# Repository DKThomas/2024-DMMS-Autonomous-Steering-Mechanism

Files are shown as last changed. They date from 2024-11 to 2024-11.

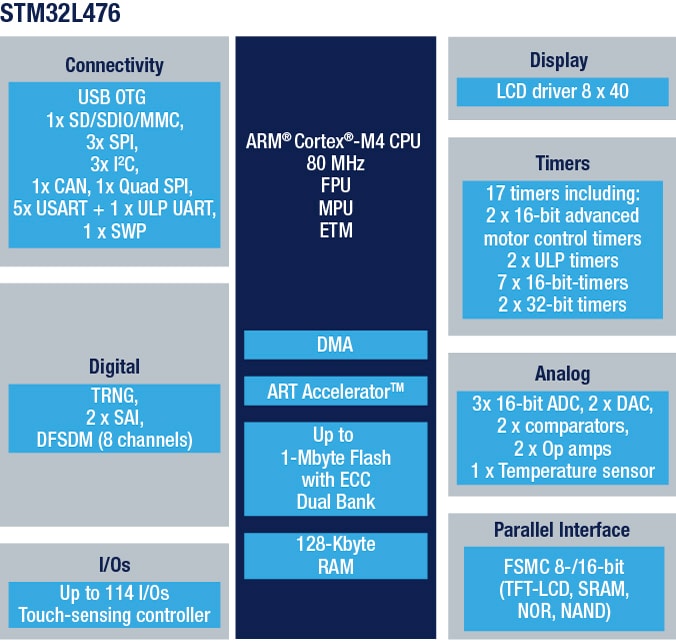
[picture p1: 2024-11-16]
Motor Control/NUCLEO-L476RG/STM32L476 Diagram.jpg

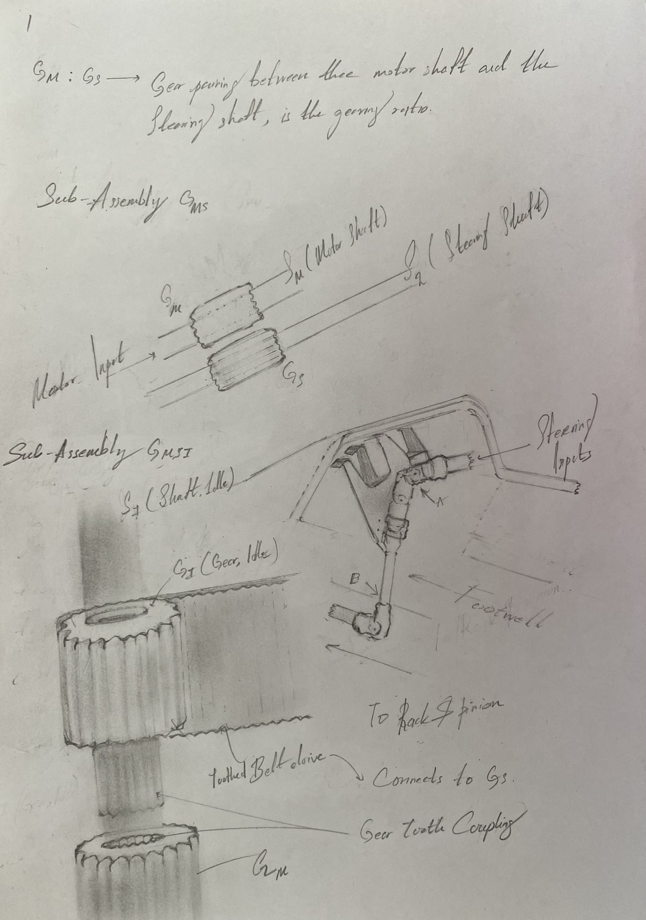
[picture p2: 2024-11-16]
Documentation/Ideation Sketches/Motor Mount/Sketch_v4.jpeg

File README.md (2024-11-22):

# **Project Overview**
Welcome to the repository for the project **Design of an autonomous steering mechanism for UTS Motorsports Autonomous** (**Project 29** by **Team 21** in **43019 Design in Mechanical and Mechatronic Systems** at **University of Technology Sydney** in **Spring 2024**). 

---

## **Folder Structure**

This repository is organized into three main folders:

### **`CAD/`**
This folder contains all CAD resources required for the project, including individual components, assembly files and installation guides.
- **`Enclosure/`**: CAD files for the protective housing of the system.
- **`FINAL design/`**: Finalized design files representing the complete system.
- **`Guide to Installation`**: Step-by-step guide for installing and assembling the mechanical system.
- **`Motor/`**: CAD models of the CubeMars AK80-9 motor.
- **`Motor Mount/`**: CAD models and technical drawings for mounting the motor.
- **`Template/`**: Driver template for compliance with FSAE rules.

### **`Documentation/`**
This folder provides insight to the development process of the project.
- **`Calculations/`**: Relevant calculations supporting the design.
- **`Competition Rules/`**: Official FSAE 2024 rules.
- **`Ideation Sketches/`**: Early conceptual sketches and ideas that led to the project’s development.
- **`Main Report`**: The primary report summarizing the project's goals, progress and results.
- **`Project Management/`**: Other project planning resources.
- **`Project Proposal`**: Initial proposal outlining the project's proposed objectives, scope, and deliverables.
- **`Reference Designs/`**: External design references used during the project’s development.

### **`Motor Control/`**
This folder focuses on the software and resources needed for motor control and implementation.
- **`AK Series Module Driver User Manual`**: User manual for the CubeMars AK series motors.
- **`Block Diagrams/`**: Visual representations of motor control architectures.
- **`Guide for CubeMars Motors`**: A practical guide for setting up and operating CubeMars motors.
- **`UTSMA_L476RG_STEERBYWIRE/`**: Source code for the motor control system for CAN communication using the STM32 NUCLEO-L476RG microcontroller.

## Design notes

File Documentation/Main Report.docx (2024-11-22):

# Autonomous Steering Mechanism

# Main Report

Client: UTS Motorsports

Detailed process documentation, including ideation, morphological table and scoring matrix to determine possible designs. This would be justified by calculations and drawings encapsulated in a report.

# Introduction

The project involves designing a mechatronic system which enables the steering mechanism on the 2022-2023 UTS Motorsports FSAE car to be controlled autonomously. The steering system consists of a steering wheel, universal joint linkages and a steering column into a worm drive steering rack.

The engineer must consider ergonomic constraints as the vehicle must be both manually and autonomously operated. Further, competition regulations must be kept in mind throughout the design process so the final solution can form part of a fully rules-compliant competition car.

Successful completion of this project allows this year’s team to migrate to the newer 2022/23 chassis and progress towards our goal of having a rules compliant autonomous Formula SAE car. The stakeholders involved include UTS Motorsports, UTS and team sponsors.

The proposed design composes of a BLDC mounted on a bracket onto the floor of the car, which is accompanied by a wedge which would help orient the motor to be parallel to the steering column. The motor is then connected via a series of gears and pulleys.

# Project Documentation

The project scope includes the following design documentation:

- Timeline
- Ideation
- Morphological Table
- Scoring Matrix

## Timeline

Below is a flow chart of the process we followed to achieve the final design.

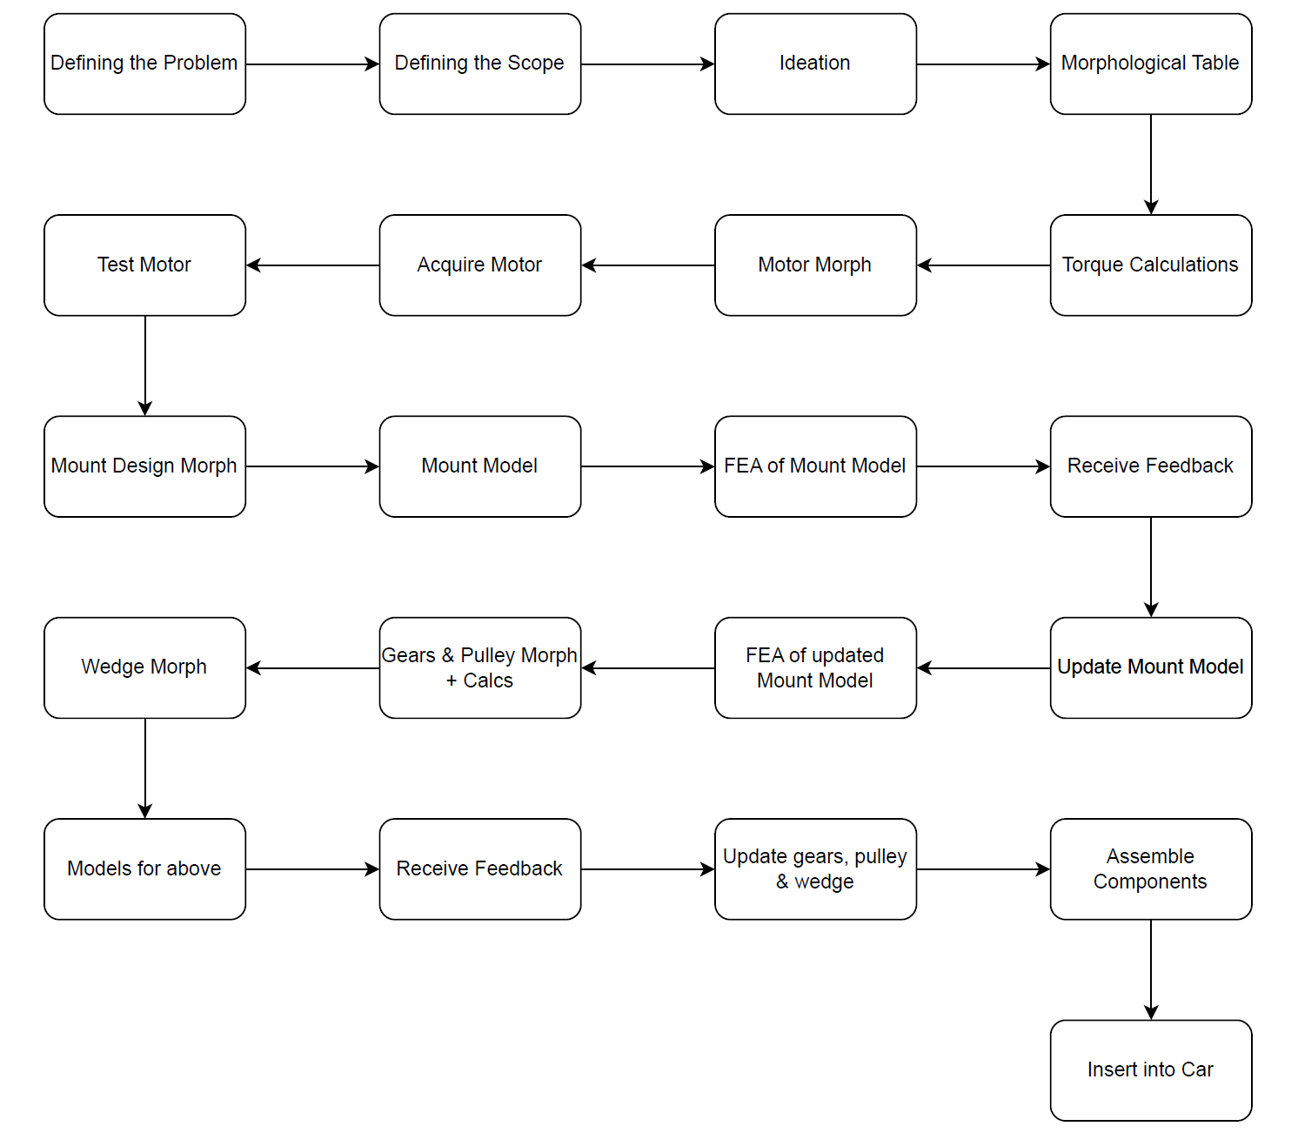
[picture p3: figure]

Figure 1: Timeline Flowchart

## Problem Statement

Design an electromechanical control system capable of rotating the steering column of the UTSMA autonomous car, ensuring it fits safely and ergonomically within the footwell while complying with the FSAE competition regulations.

## Ideation & Morphological Table

Ideating followed the basic principles of discussing how the product could be broken down into sub-assemblies which can be solved individually. These segments include:

### 1. Motor type

This was mainly condensed to two options: A BLDC or a Stepper. Finally, a BLDC Motor was selected: AK80-9.

### 2. Coupling Position

Positioned at the bottom of the steering column to make full use of space constraints with Cockpit Template (Refer to FSAE rules).

### 3. Motor to Steering Coupling

Belt and Pulley drive

### 4. Disengagement

Since the selected motor is backdrivable, the system can be electrically disengaged. Therefore, the considered idea of a mechanical disengage was discarded.

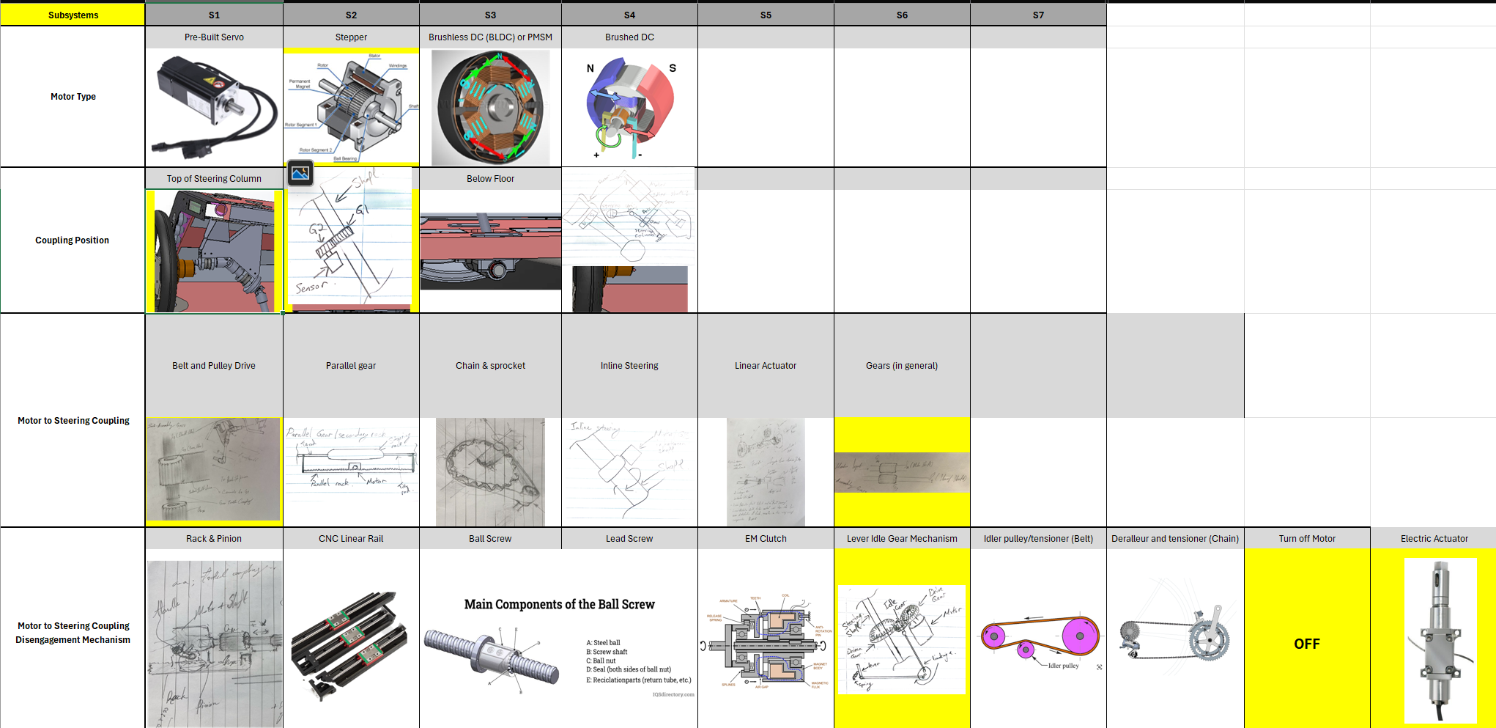
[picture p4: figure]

Figure 2: Morphological Table

## Scoring Matrix

Suitable and relevant components were selected from each of the morphological table categories and made into defined “designs”. This would be rated by the following criteria:

### 1. Performance

Delivering the calculated amount of torque without any compromise to the motor.

### 2. Precision & Accuracy

The ability of the steering system to precisely follow the desired path and make accurate adjustments.

### 3. Reliability & Durability

The system’s ability to consistently perform under various operating conditions and resist wear and tear.

### 4. Complexity & Integration

How easy the system is to design, implement, and integrate with the rest of the vehicle, including sensors, controllers, and other hardware.

### 5. Cost-Effectiveness

The overall cost of the steering system, including the cost of components, manufacturing, and maintenance.

### 6. Maintainability

The ease with which the system can be repaired, upgraded, or serviced.

### 7. Safety

Built-in safety features, fail-safes, and redundancy to prevent system failures from compromising the vehicle’s performance.

### 8. Modularity

Ease of create a modular variant, that is compliant with FSAE rules.

### 9. Scalability & Flexibility

Ease of using current design to be used in future iterations.

Using these criteria, the following design was proposed:

BLDC controlled using a magnetic rotary encoder (being positioned directly at the end of the motor shaft). It would be situated in the floor, driven by a set of gears and pulleys. The system can be disengaged by electrically disconnecting the motor, as it is backdrivable. This is shown in the figure below.

However, with a slight change in motors led to the sensor being discarded.

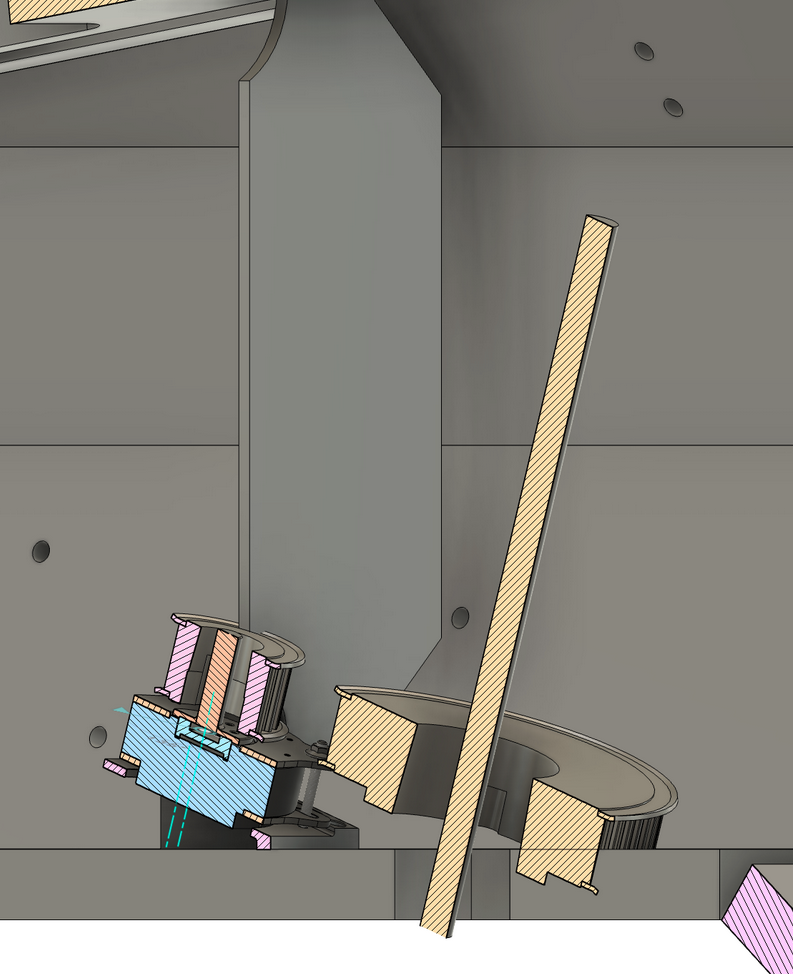
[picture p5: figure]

Figure 3: Mechanism fitted in Car Cockpit

# Issues & Feedback

- Motor torque calculations took a long time to confirm and validate, resulting in the team being able to purchase component (which has to be verified with tutor using calculations and confirmation from UTSMS) a couple of weeks in.
- Communications were not consistent in the first few weeks, which unfortunately was not completely resolved even by the end of the project.
- Issues with team members not showing up to meetings and not living up to agreements on time.
- Issues with final design not being in accordance with space constraints (refer to CAD and FSAE rules).
- Difficulty to come to decisions about final design.

# Design

## Pulley/Belt Design

This section covers the complete (for the most part) design for the belt and pulley system for the autonomous steering system.

### Determine Shaft diameters

From CAD model:

- Steering shaft column outer diameter: 15mm
- Steering shaft column inner diameter: 10mm

However, on the existing 2022 UTS Motorsports Electric car physical shaft, it is a solid 15mm steering column shaft.

Figure
CAD model close-up of shaft

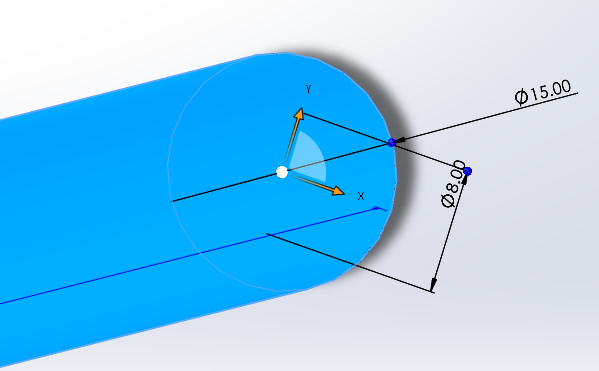
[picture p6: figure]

(Source: UTS Electric Motorsports, 2023)

Figure
Drawing of ’22 steering column

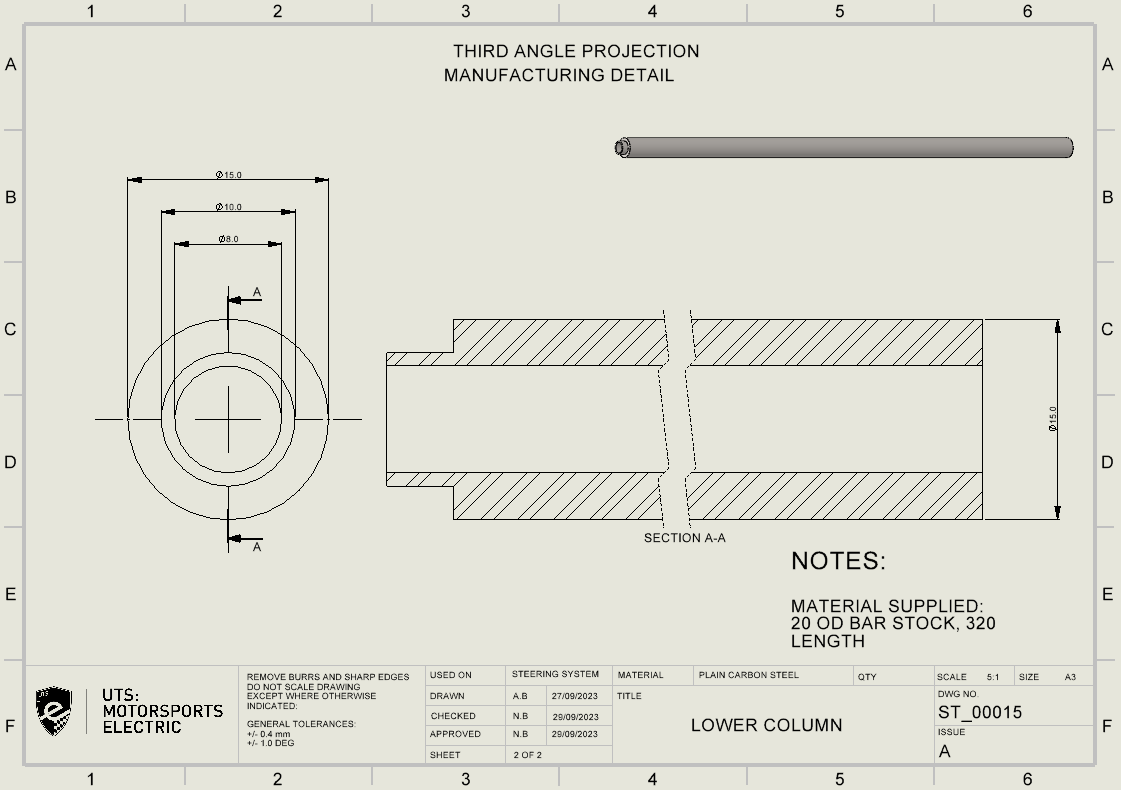
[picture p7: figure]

(Source: UTS Electric Motorsports, 2023)

From manual calculations and computer simulations:

Due to the lack of documentation, particularly with the design or the current steering system, step-by-step hand calculations were performed to analyse whether or not the current thickness of 15mm shaft diameter can support the motor’s torque. Please refer to “Analysis of Column Shaft” documentation.
Computer simulations in terms of finite element analysis (FEA) was performed to verify our hand calculations.

Motor shaft diameter:

The motor shaft of the AK1-9 motor will be customised to suit the mounting on the motor hub. The diameter of the shaft will be determined by both torsion, radial forces, along with axial forces.

Figure
Picture of AK10-9 V2.0

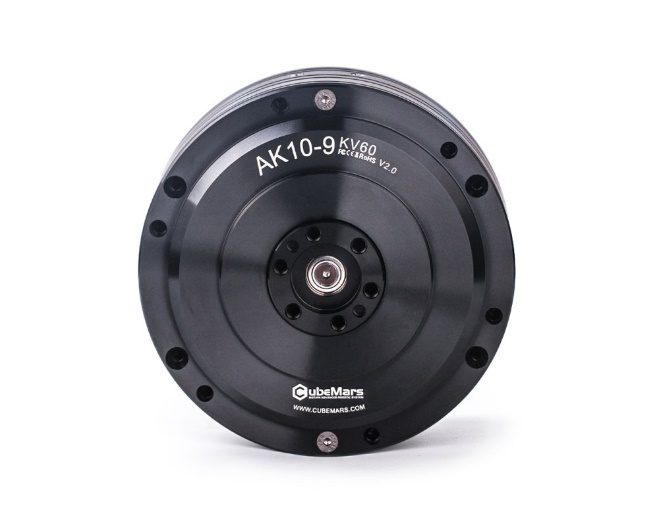
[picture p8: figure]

(Source: Tmotor, n.d)

Manual calculations and computer simulations:

Both hand calculations and FEA were performed on the design of the motor shaft. Please refer to “Analysis of Column Shaft” documentation.

### Belt Selection

There are several types of pulley belts available such as flat, V, Wedge, Synchronous belts along with other types.

Table
Comparison of Belt performance

(Source: Childs, Peter R.N.. (2014). Mechanical Design Engineering Handbook. Elsevier)

Figure
Various Belt Cross Sections

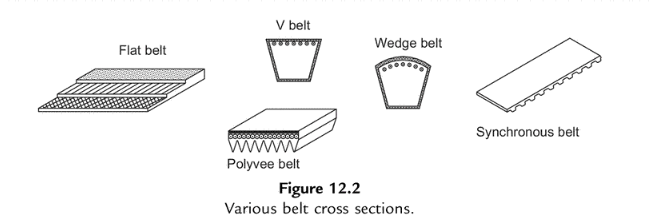
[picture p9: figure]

(Various Belts - Source: Childs, Peter R.N.. (2014). Mechanical Design Engineering Handbook. Elsevier)

Referring to the Table 12.1, synchronous belts can output an optimum efficiency of up to 98%, due to their teeth engagement between the belt teeth and the grooves of the pulley. Due to the required precise motion control of an autonomous steering system, a slippage between the belt and the pulley is highly not preferred, which the synchronous belt as the name suggests provides exact shaft synchronization (with the exception of belt creep).
Synchronous belts need significantly lower installation tension compared to V-belts, which results in reduced stress on drive components like shafts and bearings. Hence, along with the Figure 12.4, synchronous belt has been selected.

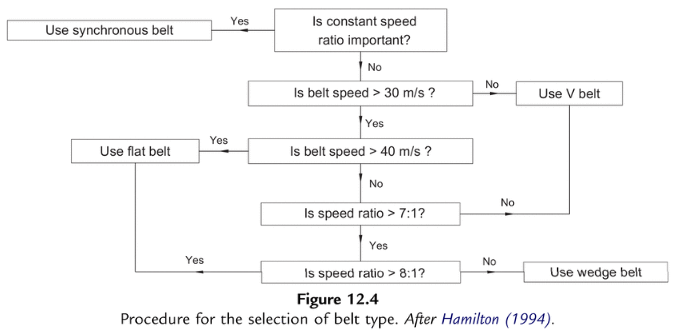
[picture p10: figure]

### General Selection Procedure – Synchronous belt pulley system

#### Define the rotational speeds of the motor shafts.

Rated motor (AK10-9 V2) speed:

- 228 rpm at 18nm (rated torque)

24.9N Steering force (With Factor of Safety of 1.5 from 16.6N steering force):
- ~200 rpm at 25nm

Motor Analysis Chart:

### 1) Pulley selection

Table
Motor Analysis Chart

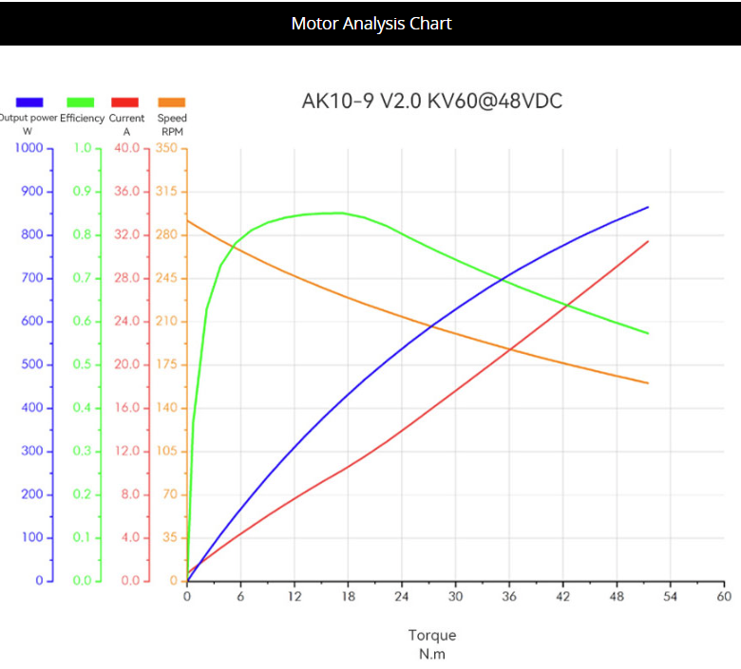
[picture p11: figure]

(Source: Tmotor, n.d)

N.m to hp:

P(HP)=(T(Nm)×N(RPM))/7127

For 18nm:

P(HP)=(18(Nm)×228(RPM))/7127 = 0.576HP

For 25nm:

P(HP)=(25(Nm)×200(RPM))/7127 = 0.702 HP

### 2) Determine the service factor.

Using Table 7-8 below, using good engineering judgement, a service factor of 1.2 has been selected.

Table
Synchronous Belt Service Factor Table

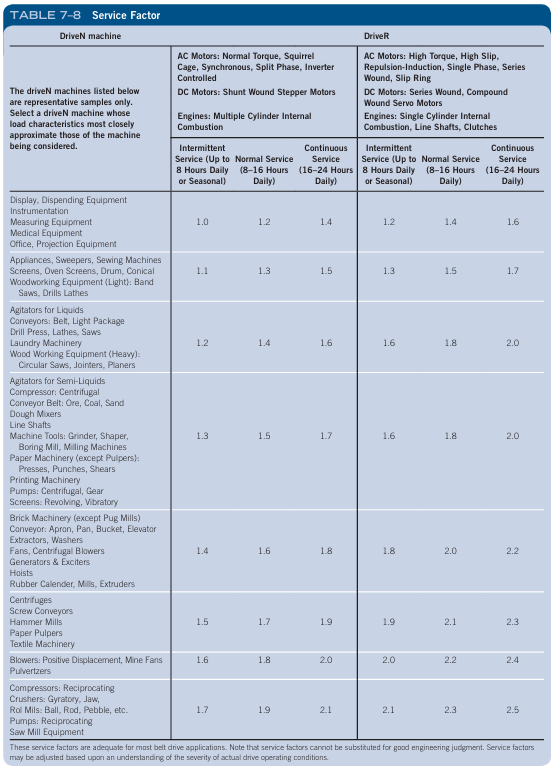
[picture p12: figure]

(Source: Mott, Robert L, 2018)

### 3) Calculate the design power.

Using the formula above;

- the design rated power is = 0.576HP x 1.2 = 0.691 HP (0.691 x 0.7457 = 0.52 kW)
- the design peak power is = 0.702 HP x 1.2 = 0.8424 HP (0.8424 x 0.7457 = 0.63kW)

1. Determine required pitch of the belt.

Graph
GT Belt Selection Guide

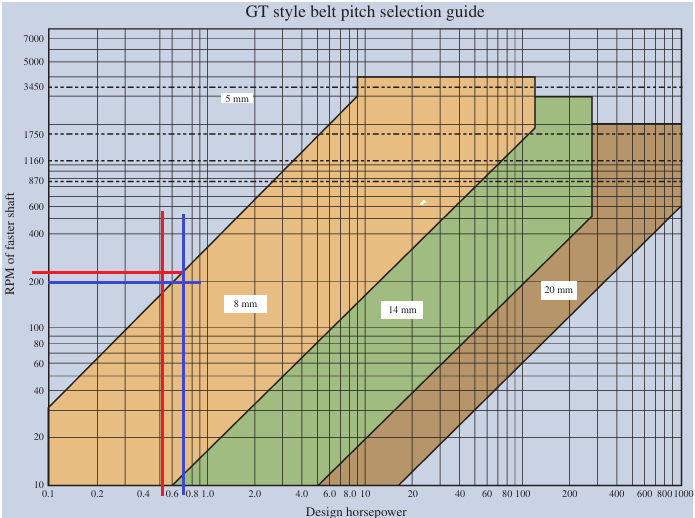
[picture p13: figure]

(Source: Mott, Robert L, 2018)

Using the table above, the red lines depict the selection for the rated torque, whilst the blue lines indicate the use of peak torque. Since the majority of the imaginary curve from the red line intersection to the blue line intersection, a 5mm belt pitch would be considered a reasonable design choice. However, 8mm had to be chosen due to belt selection requirements.

2. Determine the velocity ratio VR belt between the driver and driven sprockets.

To determine the sizes/ratio of the driven and driver pulleys, giving the following:

Motor operational torque: 18nm
Required torque: 24.9nm

An adequate pulley size ratio is needed to meet the steering force requirement of 24.9nm.

As the torque ratio is directly related to the velocity ratio:

Torque ratio = (Torque Required (Driven))/(Motor Torque (Driver))

Using the values of 24.9nm of steering torque (with FOS 1.5), with 24.9nm of required torque,

Torque ratio = (24.9 nm)/(24.9nm) ≈ 1

Therefore the driven pulley (on steering column shaft) must be 1 or more greater than the driver pulley (on the motor).

When the car is in motion, using a dynamic torque of 27nm (from 13.5N x FOS 2), At moderate dynamic or during sudden spikes:

Motor rated torque: 18nm
Required torque: 27nm

Torque ratio = (27 nm)/(18nm) ≈ 1.5

Thus, the driven pulley (attached to the steering column shaft) needs to be at least 1.38 times larger than the driver pulley (connected to the motor).

8mm Pitch Belt:

Table
Screenshot of 8mm Synchronous Belt Drive Table Part 1

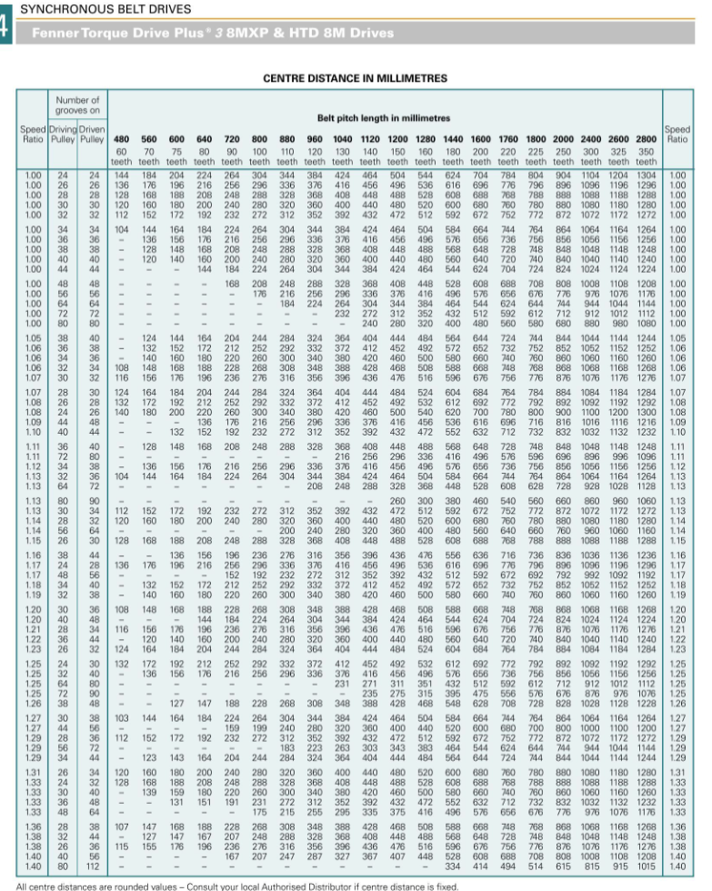
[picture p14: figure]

(Source: Fenner, 2006)

Table
Screenshot of 8mm Synchronous Belt Drive Table Part 2

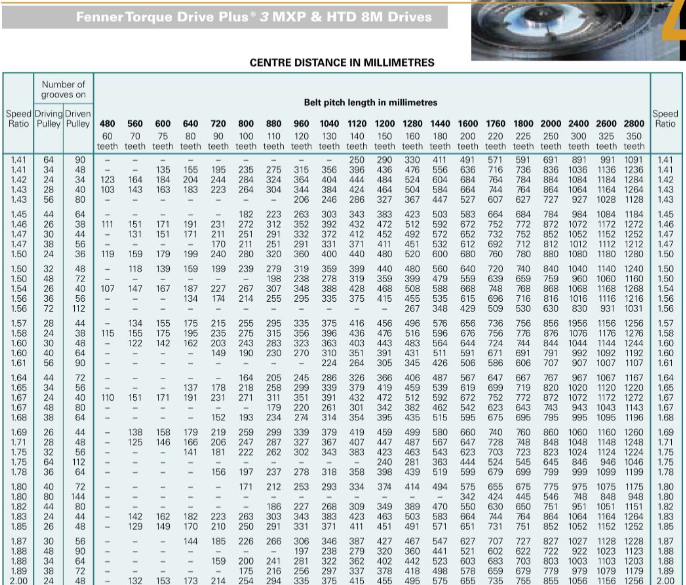
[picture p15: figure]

(Source: Fenner. 2006)

43019 DMMS T21 - P29 - Autonomous Steering Mechanism 15 Nov 2024

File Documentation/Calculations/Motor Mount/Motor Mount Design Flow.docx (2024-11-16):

Whitney, C. (2005, October 25). Sliding Motor Mount. FineWoodworking; Fine Woodworking. https://www.finewoodworking.com/2005/10/25/sliding-motor-mount

Supporting documentation for developing a Sliding Motor Mount.

Conceptual design of automobile engine rubber mounting composite using TRIZ-Morphological chart-analytic network process technique. (2018). Defence Technology, 14(4), 268–277. https://doi.org/10.1016/j.dt.2018.05.009

Information extracted (referred pages; pg. 266-270, pg. 273-275):

(1) Need for the usage (purpose) of rubber mounting – vibration dampening.

(2) Considerations when selecting material.

(3) Considerations when selecting mounting; This includes whether: (a) if a mounting is necessary,

(b) if YES, what are the relevant design/selection criteria (i.e., performance, weight, cost & etc)

(4) Criteria for weighing conceptual design (opt.)

Khan, A., Razlee, A., Zainal Nazri, Razak, A., & Ahmad, M. N. (2022). Topology Optimization of an Engine Mounting Bracket Using Finite Elements. Advanced Structured Materials, 243–254. https://doi.org/10.1007/978-3-030-93250-3_21

Information extracted (referred “Introduction”; pg. 1)

(1) FEA vs EMA
(2) Topology Optimization

(3) “x” Mount to be able to withstand, “x” load, “x” vibration/frequency.

Design and Construction of Motor Mounts. (2008). https://roblab.org/theses/2008-REV-Motor-Tan.pdf

Information extracted (referred pages; pg. 5-7, pg. 17-20. pg. 21-36):

(1) Further discussion on rubber mounting. This report discusses the general integration of rubber mounts for an engines & motors – To Dampen any resultant (BLDC) motor vibration and isolate these vibrations from the chassis.

(2) Assembly of rear support mounts, front support mounts & coupling.

(2.1) Depending on the motor, select a suitable mount design (i.e., middle-style, plate mounts)

(2.2) Motor front mounting plate/adapter design process + CNC machined, for precision using Al13.

(2.3) Coupling – TAPER LOCK HUBS (favoured) due to coupling security + ease of maintenance.

Look here for in-market options: https://www.ptparts.com.au/products/category/JADNKLMX-special-hubs/N100-TL-J-HUB--taper-lock-hubs

(3) Design options + ideation + finalisation of design (pg.)

Galloway, K. C., G. Clark Haynes, Deniz Ilhan, & Koditschek, D. (2010, November 4). X-RHex: A Highly Mobile Hexapedal Robot for Sensorimotor Tasks. ResearchGate; unknown. https://www.researchgate.net/publication/49128188_X-RHex_A_Highly_Mobile_Hexapedal_Robot_for_Sensorimotor_Tasks/figures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

Information extracted (referred pages; pg. 7-10):

(1) Spring loaded quick-release latches.
(2) Gearing offsets (opt.).

(3) Motor shaft extension.
(4) Overall motor mount design that consists of the assembly of a back plate & front plate.

Motor Mount Design Examples

1. Ideation of mounting system
2. Ideation of subsystem(s) + subsystem breakdown
2.1 Force distribution considerations (system suited to handle lateral and vertical loads)
2.1.1 Calculations/justifications for 2.1 – TBD
2.2 Decision to use tilted + angled Mount_Legs to distribute load(s) over a wider area.
2.2.1 Angle of 70 degrees, between Motor_Base_Plate & Mount_Legs (for optimal load distribution)
2.2.2 Calculations/justifications for 2.2.1 – TBD
2.2.3 FIND; Angle of ‘x’ for tilt – TBD
2.3 ALL req. dimensions for Motor_Base_Plate & Mount_Legs – TBD
2.3.1 Motor_Base_Plate “material selection” (6061, Al) – TDB; shy 2
2.3.1.1 Motor_Base_Plate spec. re-evaluation
2.3.2 Mount_Legs “material selection”
2.3.2.1 Mount_Legs spec. re-evaluation
2.4 Decision to design the Motor_Base_Plate separately + mount to Mount _Legs (for ease of handling)
2.4.1 Mounting Motor_Base_Plate to Mount _Legs
Using: External_Slotted_Flange + *Bolts + *Lock nuts + *Washers (Nord-Lock)
2.4.2 External_Slotted_Flange to be supported with Gusset_Plate(s)
2.4.3 External_Slotted_Flange with “vertical/horizontal slot” + “slot dimensions” – TBD
2.4.5 External_Slotted_Flange dimensions – TDB
2.4.4 External_Slotted_Flange “material selection” (100% infill, PLA) – TDB; shy 2
2.4.4.1 External_Slotted_Flange spec. re-evaluation
2.4.5 Gusset_Plate(s) dimensions – TDB
2.4.6 Gusset_Plate(s) “material selection” (100% infill, PLA) – TDB; shy 2
2.4.6.1 Gusset_Plate(s) spec. re-evaluation
2.4.7 *Bolts selection (for fastening Motor_Base_Plate to External_Slotted_Flange) – TBD
2.4.8 *Bolts; quantity + dimensions – TBD
2.4.9 *Lock nuts; quantity + dimensions – TBD
2.4.10 *Washers; quantity + dimensions – TBD
2.4.11 Calculations/justifications for 2.4.7 + 2.4.8 + 2.4.9 + 2.4.10 – TBD
Component List (Not complete):
Motor_Base_Plate, Mount_Legs, Motor_Base_Plate, External_Slotted_Flange, Gusset_Plate(s), *Bolts; MotorToBase_Plate_Bolt, Base_PlateToMount_Leg_Bolt, Mount_LegToFloor_Bolt *Lock nuts, *Washers

Stamp 1: Steps 1. – 5. Finding Belt Length (Distance between Motor_Shaft & Steering_Shaft)
1. Find Rated Motor torque
2. Find Req. Steering (Rack & Pinion) torque
3. Calculate “optimum pulley ratio”
4. Find Req. “Motor_Shaft_Pulley pitch + diameter” using 3.
4.1 Find Req. “Steering_Shaft_Pulley pitch + diameter” Using 3.
4.1.2 Hence; Req. “Motor_Shaft_Pulley teeth quantity”. Using 3.
4.1.3 Hence; Req. “Steering_Shaft_Pulley teeth quanitity”. Using 3.
5. Find the belt length. Therefore; “viable Motor – Steering_Shaft distance” using belt length formula (https://sudenga.com/resources/figuring-belt-lengths-and-distance-between-pulleys/)
Stamp 2: Finding Optimum Belt Parameters & Dimensions
6. Find suitable belt specifications using information in 5.
6.1 Find “belt width” – TBD
6.2 Find quanitity of “belt teeth” – TBD
6.3 Finalise belt selection – TBD

(Custom) Motor Mount Design Flow

Motor_Shaft & Steering_Shaft – Assembly

Stamp 3: Confirming Motor_Base_Plate + Mount_Legs Assembly & Positioning

7. Decide Mount_Legs “mounting position” on vehicle floor. Using 5. – TBD
8. Find Req. “motor mounting position” on Motor_Base_Plate – TBD
9. Find Req. Motor_Base_Plate “mounting position”between the Mount_Legs
10. Model motor mount + Perform FEA + CAD for Motor mount.
11. Confirm ALL “motor mounting positions”
Stamp 1: Finding Tensioner Specifications, Design & Requirements
1. Find Req. “tensioning position” (position along the belt that needs tensioning) along pulley belt
2. Tensioner specifications (temporary, Req. Tensioner_Pulley parameters). Consider info from 7.
2.1 (Justify) IS Tensioner mounted on “car_floor/motor_mount” – TBD
2.1.1 Confirms Req. Tensioner_Pulley placement along belt – TBD
2.2 Confirms Req.Tensioner_Pulley parameters – TBD
2.2.1 Tensioner_Pulley dimensions + “material selection” – TBD
2.3 Tensioner “adjustable/spring-loaded” – TBD
Stamp 2: Tensioner_Mount Design – Brief overview
2.4 Tensioner_Pulley to Tensioner_ Mount force distribution – TBD
2.5 Tensioner_ Mount “mounting position” on (+ using) outcome of 2.1 & 2.1.1

Tensioner Specifications – Brief

Pulley Design

Distance between Motor_Shaft & Steering_Shaft: https://sudenga.com/resources/figuring-belt-lengths-and-distance-between-pulleys/

Pulley & Belt calculator https://www.blocklayer.com/pulley-belt

Pulley ratio & RPM calculator: https://calculator.academy/pulley-size-calculator/

Pulley Design: https://assets-global.website-files.com/6321faa31729834cada9ee26/6321faa317298319abaa1420_B107%20Pulley%20Design%20Guidelines%2C%20Material%20and%20Finishes.pdf

Next stages – Brief overview:
Motor_Shaft req. dimensions.
Motor to Motor_Shaft *coupling
Calculations for forces acting on Motor_Shaft
(opt.) Motor_Shaft dimension + spec. re-evaluation
Motor_Shaft_InFloor_Bearing spec

Ideation Process for Motor Mounting Mechanisms (Most preferred iteration – See below; circled in RED)

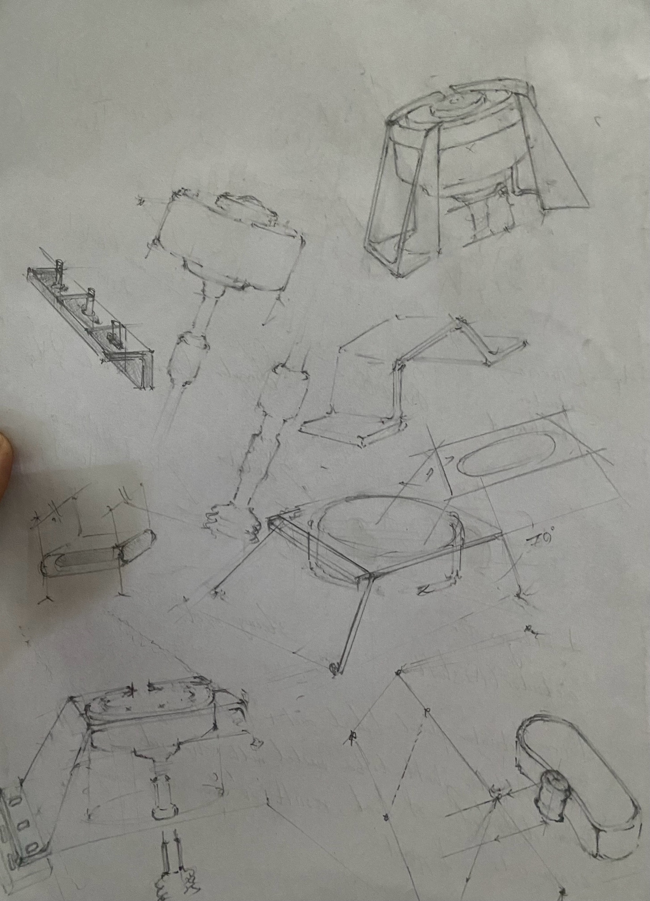
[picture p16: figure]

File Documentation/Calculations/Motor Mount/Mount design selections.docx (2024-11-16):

## Motor Mounting:

Option 1 – Angled mount (adjustable) with motor facing downwards, hole in the floor with a bearing:

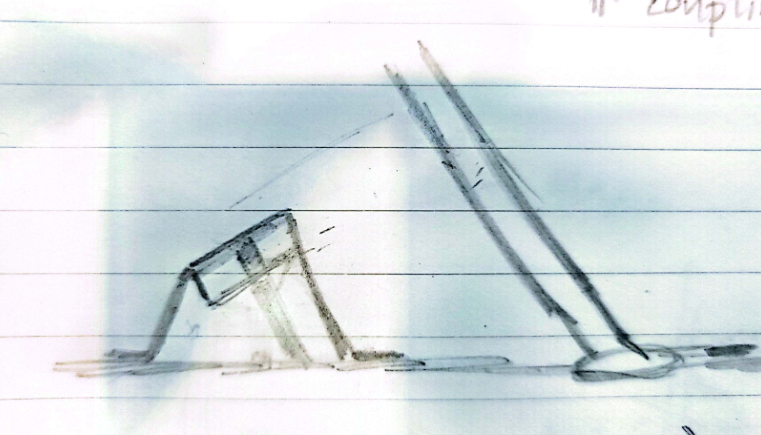
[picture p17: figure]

Option 2: Parallel mount (adjustable), motor facing downwards, U-joint with bearing (Information, despite the detail presented on the sketch below, it is important to note that the motor will be mounted atop the base mount)

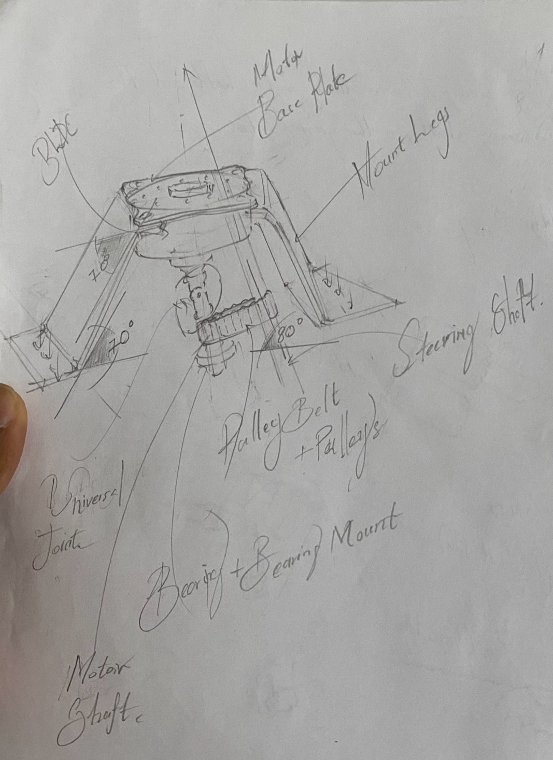
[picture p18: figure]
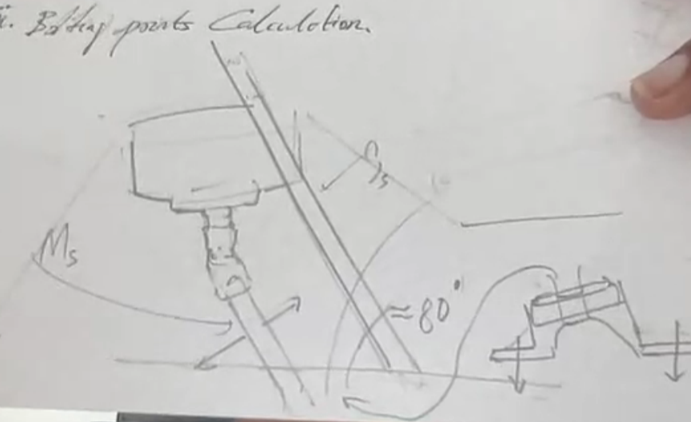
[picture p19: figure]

Option 3: Angled mount (adjustable) motor facing upwards.

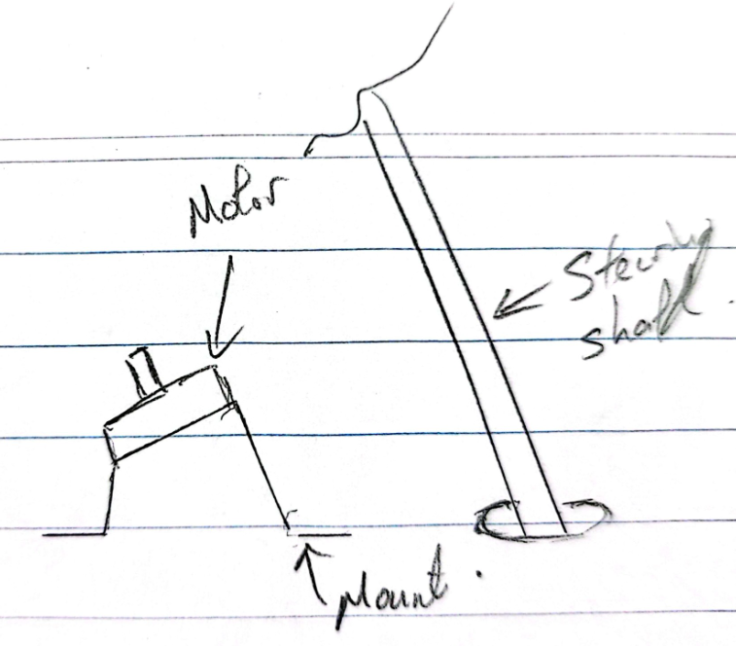
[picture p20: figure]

## Adjustable Mechanism:

Option 1:

Option 2:

Option 3:

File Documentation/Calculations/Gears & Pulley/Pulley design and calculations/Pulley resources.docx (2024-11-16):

Solidworks Belt tutorial:

https://www.youtube.com/watch?v=J5c3EpZYS3Y

https://www.youtube.com/watch?v=hBewTs1fLto

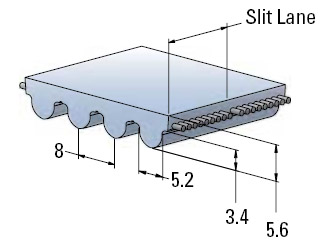
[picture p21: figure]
Dimensional drawing

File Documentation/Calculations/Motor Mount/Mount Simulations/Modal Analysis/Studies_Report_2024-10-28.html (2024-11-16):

Image Width (pixels):

# Study Report

Analyzed File | Mount_Legs v3_Mod v2 v90
Version | Autodesk Fusion (2.0.20494)
Creation Date | 2024-10-28, 17:47:54
Author | dulnethweerasinghe

#### Report Properties

Title | Studies
Author | dulnethweerasinghe

## Simulation Model 1

### Study 10 - Modal Frequencies

##### Study Properties

Study Type | Modal Frequencies
Last Modification Date | 2024-10-28, 15:54:26

#### Settings

##### General

Contact Tolerance | 0.05 mm
Number of Modes | 12
Frequency Range [Hz] | 5-50
Compute Preloaded Modes | Yes

##### Mesh

Average Element Size (% of model size)
Solids | 4
Scale Mesh Size Per Part | Yes
Average Element Size (absolute value) | -
Element Order | Parabolic
Create Curved Mesh Elements | Yes
Max. Turn Angle on Curves (Deg.) | 25
Max. Adjacent Mesh Size Ratio | 1.5
Max. Aspect Ratio | 10
Minimum Element Size (% of average size) | 10

##### Adaptive Mesh Refinement

Number of Refinement Steps | 2
Results Convergence Tolerance (%) | 20
Frequency Mode | 12

#### Materials

Component | Material | Safety Factor
Body2 | Steel, Mild | Yield Strength
Indented Hex Flange Head Machine Screw ANSI B18.6.7M - M5x0.8 x 40 Steel Grade 2 Plain v1:1 | Steel Grade 2, Plain | Yield Strength
Indented Hex Flange Head Machine Screw ANSI B18.6.7M - M5x0.8 x 40 Steel Grade 2 Plain v1:2 | Steel Grade 2, Plain | Yield Strength
Indented Hex Flange Head Machine Screw ANSI B18.6.7M - M5x0.8 x 40 Steel Grade 2 Plain v1:3 | Steel Grade 2, Plain | Yield Strength
Indented Hex Flange Head Machine Screw ANSI B18.6.7M - M5x0.8 x 40 Steel Grade 2 Plain v1:4 | Steel Grade 2, Plain | Yield Strength
Hex Flange Nut ANSI B18.2.4.4M - M5 x 0.8 Steel Grade 2H Plain v1:1 | Steel Grade 2H, Plain | Yield Strength
Hex Flange Nut ANSI B18.2.4.4M - M5 x 0.8 Steel Grade 2H Plain v1:2 | Steel Grade 2H, Plain | Yield Strength
Hex Flange Nut ANSI B18.2.4.4M - M5 x 0.8 Steel Grade 2H Plain v1:3 | Steel Grade 2H, Plain | Yield Strength
Hex Flange Nut ANSI B18.2.4.4M - M5 x 0.8 Steel Grade 2H Plain v1:4 | Steel Grade 2H, Plain | Yield Strength

##### Steel Grade 2, Plain

Density | 7.750E-06 kg / mm^3
Young's Modulus | 210000.00 MPa
Poisson's Ratio | 0.30
Yield Strength | 393.00 MPa
Ultimate Tensile Strength | 510.00 MPa
Thermal Conductivity | 0.056 W / (mm C)
Thermal Expansion Coefficient | 1.200E-05 / C
Specific Heat | 480.00 J / (kg C)

##### Steel Grade 2H, Plain

Density | 7.750E-06 kg / mm^3
Young's Modulus | 210000.00 MPa
Poisson's Ratio | 0.30
Yield Strength | 393.00 MPa
Ultimate Tensile Strength | 510.00 MPa
Thermal Conductivity | 0.056 W / (mm C)
Thermal Expansion Coefficient | 1.200E-05 / C
Specific Heat | 480.00 J / (kg C)

##### Steel, Mild

Density | 7.850E-06 kg / mm^3
Young's Modulus | 220000.00 MPa
Poisson's Ratio | 0.275
Yield Strength | 207.00 MPa
Ultimate Tensile Strength | 345.00 MPa
Thermal Conductivity | 0.045 W / (mm C)
Thermal Expansion Coefficient | 1.200E-05 / C
Specific Heat | 480.00 J / (kg C)

#### Contacts

#### Mesh

Type | Nodes | Elements
Solids | 284087 | 159634

#### Load Case1

 Solve result of this load case is out of date.

#### Constraints

##### Fixed1

Type | Fixed
Ux | Fixed
Uy | Fixed
Uz | Fixed

###### Selected Entities

For correct interpretation of this image use e.g. IE9, Chrome, Safari, Firefox

#### Loads

##### Gravity

Type | Gravity
Magnitude | 9.807 m / s^2
X Value | 0.00 m / s^2
Y Value | 0.00 m / s^2
Z Value | -9.807 m / s^2

###### Selected Entities

For correct interpretation of this image use e.g. IE9, Chrome, Safari, Firefox

#### Results

##### Result Summary

Frequency | Participation X | Participation Y | Participation Z
Mode 1: 352.514 Hz | 53.7701011 | 0 | 0.0032

##### Total Modal Displacement

###### Mode 1: 352.514 Hz Total Modal Displacement

0.00 1.00

For correct interpretation of this image use e.g. IE9, Chrome, Safari, Firefox

Image Width (pixels):

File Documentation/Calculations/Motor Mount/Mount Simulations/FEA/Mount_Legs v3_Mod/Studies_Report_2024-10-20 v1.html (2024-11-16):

Image Width (pixels):

# Study Report

Analyzed File | Mount_Legs v3_Mod v4
Version | Autodesk Fusion (2.0.20476)
Creation Date | 2024-10-20, 01:47:26
Author | dulnethweerasinghe

#### Report Properties

Title | Studies
Author | dulnethweerasinghe

## Simulation Model 1

### Study 6 - Static Stress

##### Study Properties

Study Type | Static Stress
Last Modification Date | 2024-10-20, 01:38:45

#### Settings

##### General

Contact Tolerance | 0.05 mm
Remove Rigid Body Modes | No

##### Mesh

Average Element Size (% of model size)
Solids | 3
Scale Mesh Size Per Part | No
Average Element Size (absolute value) | -
Element Order | Parabolic
Create Curved Mesh Elements | No
Max. Turn Angle on Curves (Deg.) | 60
Max. Adjacent Mesh Size Ratio | 1.5
Max. Aspect Ratio | 10
Minimum Element Size (% of average size) | 20

##### Adaptive Mesh Refinement

Number of Refinement Steps | 0
Results Convergence Tolerance (%) | 20
Portion of Elements to Refine (%) | 10
Results for Baseline Accuracy | von Mises Stress

#### Materials

Component | Material | Safety Factor
Body2 | Aluminum 6061 | Yield Strength
Indented Hex Flange Head Machine Screw ANSI B18.6.7M - M6x1 x 20 Steel Grade 2 Plain v1:2 | Steel Grade 2, Plain | Yield Strength
Indented Hex Flange Head Machine Screw ANSI B18.6.7M - M6x1 x 20 Steel Grade 2 Plain v1:3 | Steel Grade 2, Plain | Yield Strength
Indented Hex Flange Head Machine Screw ANSI B18.6.7M - M6x1 x 20 Steel Grade 2 Plain v1:4 | Steel Grade 2, Plain | Yield Strength
Indented Hex Flange Head Machine Screw ANSI B18.6.7M - M6x1 x 20 Steel Grade 2 Plain v1:1 | Steel Grade 2, Plain | Yield Strength

##### Steel Grade 2, Plain

Density | 7.750E-06 kg / mm^3
Young's Modulus | 210000.00 MPa
Poisson's Ratio | 0.30
Yield Strength | 393.00 MPa
Ultimate Tensile Strength | 510.00 MPa
Thermal Conductivity | 0.056 W / (mm C)
Thermal Expansion Coefficient | 1.200E-05 / C
Specific Heat | 480.00 J / (kg C)

##### Aluminum 6061

Density | 2.700E-06 kg / mm^3
Young's Modulus | 68900.00 MPa
Poisson's Ratio | 0.33
Yield Strength | 275.00 MPa
Ultimate Tensile Strength | 310.00 MPa
Thermal Conductivity | 0.167 W / (mm C)
Thermal Expansion Coefficient | 2.360E-05 / C
Specific Heat | 897.00 J / (kg C)

#### Contacts

##### Bonded

Name

[S] Bonded5 [Simulation Model 1:1||Indented Hex Flange Head Machine Screw ANSI B18.6.7M - M6x1 x 20 Steel Grade 2 Plain v1:4]

[S] Bonded6 [Simulation Model 1:1||Indented Hex Flange Head Machine Screw ANSI B18.6.7M - M6x1 x 20 Steel Grade 2 Plain v1:3]

[S] Bonded7 [Simulation Model 1:1||Indented Hex Flange Head Machine Screw ANSI B18.6.7M - M6x1 x 20 Steel Grade 2 Plain v1:2]

[S] Bonded8 [Simulation Model 1:1||Indented Hex Flange Head Machine Screw ANSI B18.6.7M - M6x1 x 20 Steel Grade 2 Plain v1:1]

[S] Bonded10 [Simulation Model 1:1||Indented Hex Flange Head Machine Screw ANSI B18.6.7M - M6x1 x 20 Steel Grade 2 Plain v1:4]

[S] Bonded11 [Simulation Model 1:1||Indented Hex Flange Head Machine Screw ANSI B18.6.7M - M6x1 x 20 Steel Grade 2 Plain v1:1]

#### Mesh

Type | Nodes | Elements
Solids | 108271 | 63075

#### Load Case1

#### Constraints

##### Fixed1

Type | Fixed
Ux | Fixed
Uy | Fixed
Uz | Fixed

###### Selected Entities

For correct interpretation of this image use e.g. IE9, Chrome, Safari, Firefox

#### Loads

##### Gravity

Type | Gravity
Magnitude | 9.807 m / s^2
X Value | 0.00 m / s^2
Y Value | 0.00 m / s^2
Z Value | -9.807 m / s^2

###### Selected Entities

For correct interpretation of this image use e.g. IE9, Chrome, Safari, Firefox

##### Force1

Type | Force
Magnitude | 8.00 N
X Value | 0.00 N
Y Value | 0.00 N
Z Value | -8.00 N
Force Per Entity | No

###### Selected Entities

For correct interpretation of this image use e.g. IE9, Chrome, Safari, Firefox

##### Moment1

Type | Moment
Magnitude | 20000.00 N mm
X Value | 0.00 N mm
Y Value | 0.00 N mm
Z Value | -20000.00 N mm
X Angle | 0.0 deg
Y Angle | 90.0 deg
Z Angle | 0.0 deg

###### Selected Entities

For correct interpretation of this image use e.g. IE9, Chrome, Safari, Firefox

##### Moment2

Type | Moment
Magnitude | 20000.00 N mm
X Value | 0.00 N mm
Y Value | 0.00 N mm
Z Value | -20000.00 N mm
X Angle | 0.0 deg
Y Angle | 90.0 deg
Z Angle | 0.0 deg

###### Selected Entities

For correct interpretation of this image use e.g. IE9, Chrome, Safari, Firefox

#### Results

##### Result Summary

Name | Minimum | Maximum
Safety Factor
Safety Factor (Per Body) | 4.819 | 15.00
Stress
von Mises | 0.01 MPa | 57.07 MPa
1st Principal | -34.019 MPa | 92.325 MPa
3rd Principal | -86.913 MPa | 35.275 MPa
Normal XX | -75.346 MPa | 81.357 MPa
Normal YY | -46.568 MPa | 48.774 MPa
Normal ZZ | -43.483 MPa | 44.66 MPa
Shear XY | -19.922 MPa | 19.801 MPa
Shear YZ | -12.539 MPa | 19.236 MPa
Shear ZX | -25.756 MPa | 20.067 MPa
Displacement
Total | 0.00 mm | 0.051 mm
X | -0.03 mm | 0.025 mm
Y | -0.024 mm | 0.032 mm
Z | -0.031 mm | 0.033 mm
Reaction Force
Total | 0.00 N | 89.701 N
X | -80.565 N | 69.68 N
Y | -34.406 N | 29.424 N
Z | -36.039 N | 41.484 N
Strain
Equivalent | 0.00 | 0.001
1st Principal | -2.131E-07 | 0.001
3rd Principal | -0.001 | 0.00
Normal XX | -7.805E-04 | 8.154E-04
Normal YY | -2.110E-04 | 2.472E-04
Normal ZZ | -2.122E-04 | 2.136E-04
Shear XY | -7.691E-04 | 7.644E-04
Shear YZ | -4.841E-04 | 3.686E-04
Shear ZX | -7.641E-04 | 7.495E-04
Contact Pressure
Total | 0.00 MPa | 21.643 MPa
X | -13.313 MPa | 18.089 MPa
Y | -20.048 MPa | 9.159 MPa
Z | -8.654 MPa | 17.217 MPa
Contact Force
Total | 0.00 N | 9.094 N
X | -5.931 N | 5.789 N
Y | -3.795 N | 2.059 N
Z | -8.942 N | 7.76 N

##### Safety Factor

###### Safety Factor (Per Body)

0.00 8.00

For correct interpretation of this image use e.g. IE9, Chrome, Safari, Firefox

##### Stress

###### von Mises

[MPa] 0.01 57.07

For correct interpretation of this image use e.g. IE9, Chrome, Safari, Firefox

###### 1st Principal

[MPa] -34.019 92.325

For correct interpretation of this image use e.g. IE9, Chrome, Safari, Firefox

###### 3rd Principal

[MPa] -86.913 35.275

For correct interpretation of this image use e.g. IE9, Chrome, Safari, Firefox

##### Displacement

###### Total

[mm] 0.00 0.051

For correct interpretation of this image use e.g. IE9, Chrome, Safari, Firefox

#### Load Case2

#### Constraints

##### Fixed2

Type | Fixed
Ux | Fixed
Uy | Fixed
Uz | Fixed

###### Selected Entities

#### Loads

##### Gravity

Type | Gravity
Magnitude | 9.807 m / s^2
X Value | 0.00 m / s^2
Y Value | 0.00 m / s^2
Z Value | -9.807 m / s^2

###### Selected Entities

##### Moment3

Type | Moment
Magnitude | 11000.00 N mm
X Value | 0.00 N mm
Y Value | 0.00 N mm
Z Value | -11000.00 N mm
X Angle | 0.0 deg
Y Angle | 90.0 deg
Z Angle | 0.0 deg

###### Selected Entities

##### Moment4

Type | Moment
Magnitude | 12000.00 N mm
X Value | 0.00 N mm
Y Value | 0.00 N mm
Z Value | 12000.00 N mm
X Angle | 0.0 deg
Y Angle | -90.0 deg
Z Angle | 0.0 deg

###### Selected Entities

For correct interpretation of this image use e.g. IE9, Chrome, Safari, Firefox

##### Force2

Type | Force
Magnitude | 10.00 N
X Value | 0.00 N
Y Value | 0.00 N
Z Value | -10.00 N
Force Per Entity | No

###### Selected Entities

#### Results

##### Result Summary

Name | Minimum | Maximum
Safety Factor
Safety Factor (Per Body) | 14.186 | 15.00
Stress
von Mises | 0.003 MPa | 27.703 MPa
1st Principal | -8.825 MPa | 38.137 MPa
3rd Principal | -36.789 MPa | 9.306 MPa
Normal XX | -20.005 MPa | 22.936 MPa
Normal YY | -19.865 MPa | 17.557 MPa
Normal ZZ | -24.206 MPa | 23.982 MPa
Shear XY | -7.959 MPa | 8.218 MPa
Shear YZ | -2.858 MPa | 10.988 MPa
Shear ZX | -14.164 MPa | 11.623 MPa
Displacement
Total | 0.00 mm | 0.007 mm
X | -0.004 mm | 0.003 mm
Y | -0.001 mm | 0.004 mm
Z | -0.005 mm | 0.004 mm
Reaction Force
Total | 0.00 N | 12.526 N
X | -10.954 N | 10.412 N
Y | -5.026 N | 4.172 N
Z | -4.939 N | 6.351 N
Strain
Equivalent | 0.00 | 2.285E-04
1st Principal | 0.00 | 2.573E-04
3rd Principal | -2.538E-04 | 1.903E-07
Normal XX | -1.193E-04 | 1.226E-04
Normal YY | -6.784E-05 | 9.615E-05
Normal ZZ | -9.122E-05 | 8.470E-05
Shear XY | -1.221E-04 | 1.147E-04
Shear YZ | -9.183E-05 | 1.360E-04
Shear ZX | -1.754E-04 | 1.439E-04
Contact Pressure
Total | 0.00 MPa | 10.454 MPa
X | -7.77 MPa | 6.454 MPa
Y | -9.908 MPa | 5.143 MPa
Z | -5.543 MPa | 8.753 MPa
Contact Force
Total | 0.00 N | 3.595 N
X | -2.132 N | 2.828 N
Y | -2.219 N | 0.847 N
Z | -2.01 N | 2.363 N

##### Safety Factor

###### Safety Factor (Per Body)

0.00 8.00

For correct interpretation of this image use e.g. IE9, Chrome, Safari, Firefox

##### Stress

###### von Mises

[MPa] 0.003 27.703

For correct interpretation of this image use e.g. IE9, Chrome, Safari, Firefox

###### 1st Principal

[MPa] -8.825 38.137

For correct interpretation of this image use e.g. IE9, Chrome, Safari, Firefox

###### 3rd Principal

[MPa] -36.789 9.306

For correct interpretation of this image use e.g. IE9, Chrome, Safari, Firefox

##### Displacement

###### Total

[mm] 0.00 0.007

For correct interpretation of this image use e.g. IE9, Chrome, Safari, Firefox

Image Width (pixels):

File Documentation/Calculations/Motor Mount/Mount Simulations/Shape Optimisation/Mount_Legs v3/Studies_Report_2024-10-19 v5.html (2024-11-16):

Image Width (pixels):

# Study Report

Analyzed File | Mount_Legs v3 v15
Version | Autodesk Fusion (2.0.20476)
Creation Date | 2024-10-19, 19:10:15
Author | dulnethweerasinghe

#### Report Properties

Title | Studies
Author | dulnethweerasinghe

## Simulation Model 1

### Study 3 - Shape Optimization

##### Study Properties

Study Type | Shape Optimization
Last Modification Date | 2024-10-19, 18:56:49

#### Settings

##### General

Contact Tolerance | 0.05 mm
Remove Rigid Body Modes | No

##### Mesh

Average Element Size (% of model size)
Solids | 3
Scale Mesh Size Per Part | No
Average Element Size (absolute value) | -
Element Order | Linear
Create Curved Mesh Elements | No
Max. Turn Angle on Curves (Deg.) | 60
Max. Adjacent Mesh Size Ratio | 1.5
Max. Aspect Ratio | 10
Minimum Element Size (% of average size) | 20

#### Materials

Component | Material | Safety Factor
Body2 | Aluminum 6061 | Yield Strength
Indented Hex Flange Head Machine Screw ANSI B18.6.7M - M6x1 x 20 Steel Grade 2 Plain v1:1 | Steel Grade 2, Plain | Yield Strength
Indented Hex Flange Head Machine Screw ANSI B18.6.7M - M6x1 x 20 Steel Grade 2 Plain v1:2 | Steel Grade 2, Plain | Yield Strength
Indented Hex Flange Head Machine Screw ANSI B18.6.7M - M6x1 x 20 Steel Grade 2 Plain v1:3 | Steel Grade 2, Plain | Yield Strength
Indented Hex Flange Head Machine Screw ANSI B18.6.7M - M6x1 x 20 Steel Grade 2 Plain v1:4 | Steel Grade 2, Plain | Yield Strength

##### Steel Grade 2, Plain

Density | 7.750E-06 kg / mm^3
Young's Modulus | 210000.00 MPa
Poisson's Ratio | 0.30
Yield Strength | 393.00 MPa
Ultimate Tensile Strength | 510.00 MPa
Thermal Conductivity | 0.056 W / (mm C)
Thermal Expansion Coefficient | 1.200E-05 / C
Specific Heat | 480.00 J / (kg C)

##### Aluminum 6061

Density | 2.700E-06 kg / mm^3
Young's Modulus | 68900.00 MPa
Poisson's Ratio | 0.33
Yield Strength | 275.00 MPa
Ultimate Tensile Strength | 310.00 MPa
Thermal Conductivity | 0.167 W / (mm C)
Thermal Expansion Coefficient | 2.360E-05 / C
Specific Heat | 897.00 J / (kg C)

#### Contacts

##### Bonded

Name

[S] Bonded1 [Simulation Model 1:1||Indented Hex Flange Head Machine Screw ANSI B18.6.7M - M6x1 x 20 Steel Grade 2 Plain v1:3]

[S] Bonded2 [Simulation Model 1:1||Indented Hex Flange Head Machine Screw ANSI B18.6.7M - M6x1 x 20 Steel Grade 2 Plain v1:2]

[S] Bonded3 [Simulation Model 1:1||Indented Hex Flange Head Machine Screw ANSI B18.6.7M - M6x1 x 20 Steel Grade 2 Plain v1:4]

[S] Bonded4 [Simulation Model 1:1||Indented Hex Flange Head Machine Screw ANSI B18.6.7M - M6x1 x 20 Steel Grade 2 Plain v1:1]

[S] Bonded5 [Simulation Model 1:1||Indented Hex Flange Head Machine Screw ANSI B18.6.7M - M6x1 x 20 Steel Grade 2 Plain v1:4]

[S] Bonded6 [Simulation Model 1:1||Indented Hex Flange Head Machine Screw ANSI B18.6.7M - M6x1 x 20 Steel Grade 2 Plain v1:3]

[S] Bonded7 [Simulation Model 1:1||Indented Hex Flange Head Machine Screw ANSI B18.6.7M - M6x1 x 20 Steel Grade 2 Plain v1:2]

[S] Bonded8 [Simulation Model 1:1||Indented Hex Flange Head Machine Screw ANSI B18.6.7M - M6x1 x 20 Steel Grade 2 Plain v1:1]

#### Mesh

Type | Nodes | Elements
Solids | 14695 | 54978

#### Shape Optimization

#### Criteria

Parameter | Expression | Value
Target Mass | < OR = | Auto
Stiffness | Maximize

#### Results

##### Optimization Summary

Name | Value
Mass before | 0.438 kg
Mass after | 0.322 kg
Mass Ratio | 73.61 %

#### Load Case1

#### Constraints

##### Fixed1

Type | Fixed
Ux | Fixed
Uy | Fixed
Uz | Fixed

###### Selected Entities

For correct interpretation of this image use e.g. IE9, Chrome, Safari, Firefox

#### Loads

##### Gravity

Type | Gravity
Magnitude | 9.807 m / s^2
X Value | 0.00 m / s^2
Y Value | 0.00 m / s^2
Z Value | -9.807 m / s^2

###### Selected Entities

For correct interpretation of this image use e.g. IE9, Chrome, Safari, Firefox

##### Force1

Type | Force
Magnitude | 9.00 N
X Value | 0.00 N
Y Value | 0.00 N
Z Value | -9.00 N
Force Per Entity | No

###### Selected Entities

For correct interpretation of this image use e.g. IE9, Chrome, Safari, Firefox

##### Moment1

Type | Moment
Magnitude | 20000.00 N mm
X Value | 0.00 N mm
Y Value | 0.00 N mm
Z Value | 20000.00 N mm

###### Selected Entities

For correct interpretation of this image use e.g. IE9, Chrome, Safari, Firefox

##### Moment2

Type | Moment
Magnitude | 20000.00 N mm
X Value | 0.00 N mm
Y Value | 0.00 N mm
Z Value | 20000.00 N mm
X Angle | 0.0 deg
Y Angle | -90.0 deg
Z Angle | 0.0 deg

###### Selected Entities

For correct interpretation of this image use e.g. IE9, Chrome, Safari, Firefox

Image Width (pixels):

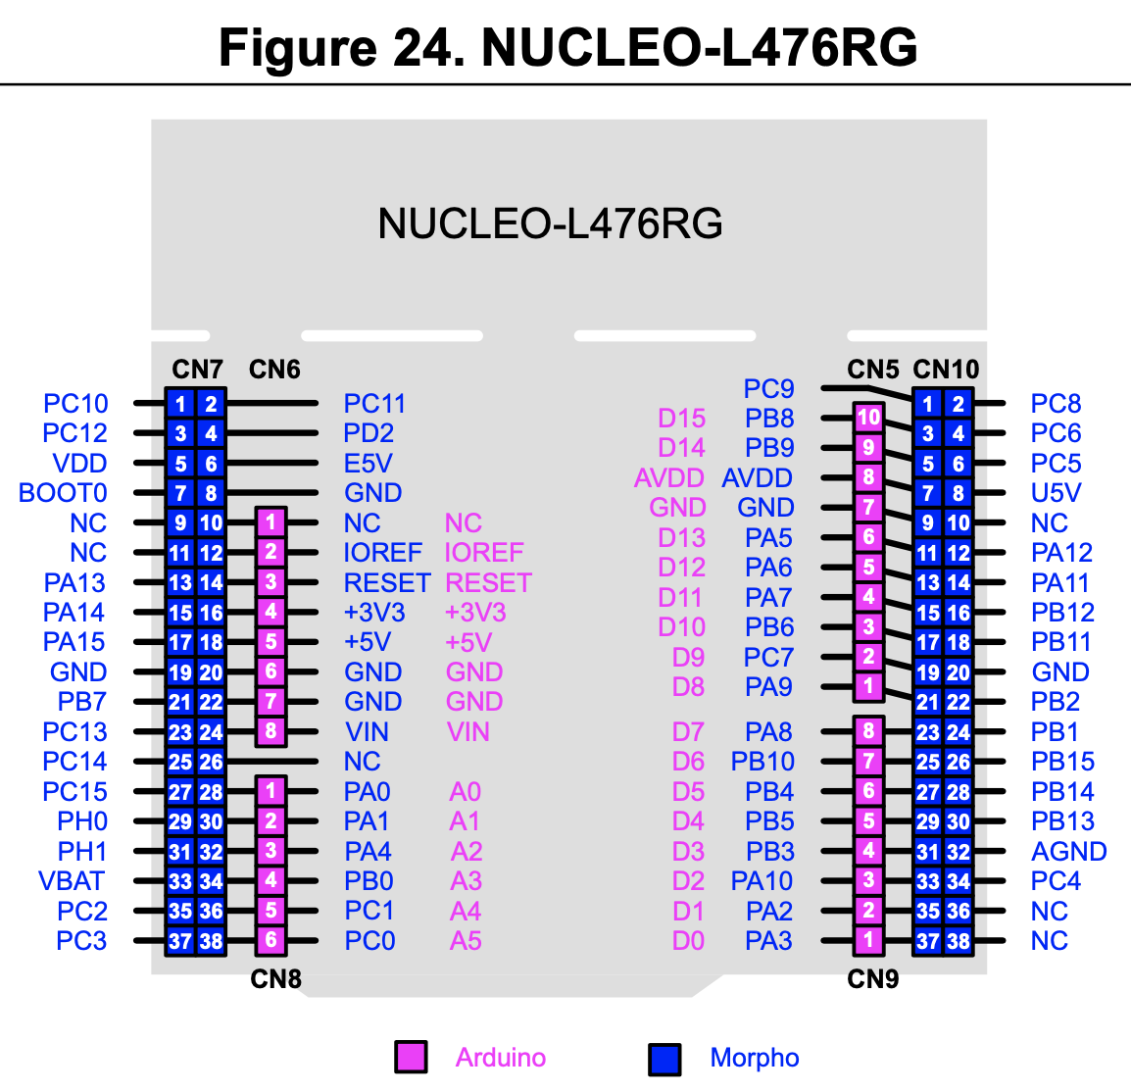
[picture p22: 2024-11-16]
Motor Control/NUCLEO-L476RG/NUCLEO-L476RG Pinout.png

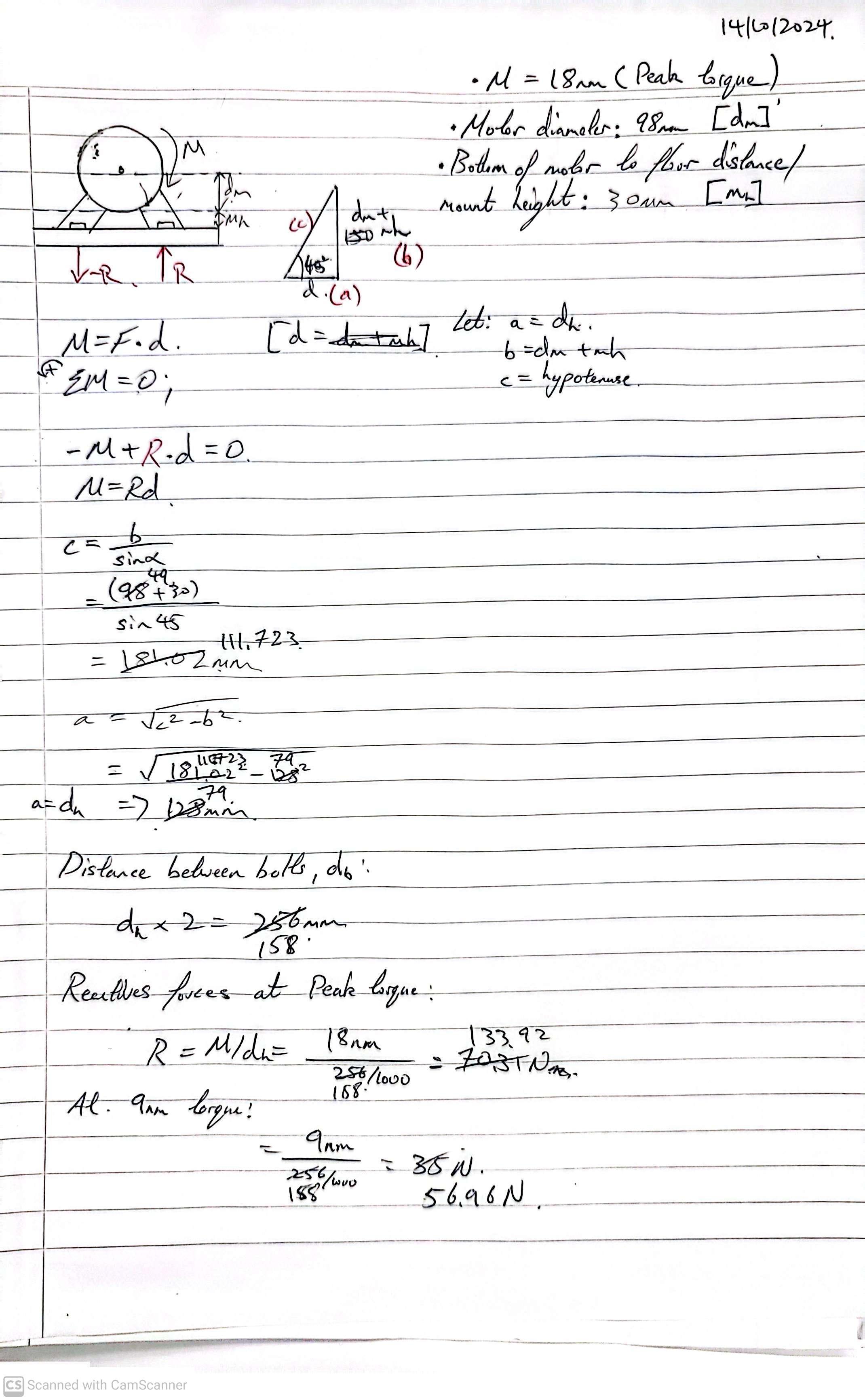
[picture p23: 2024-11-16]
Documentation/Calculations/Steering/Steering Bolt calculations Axial.jpg

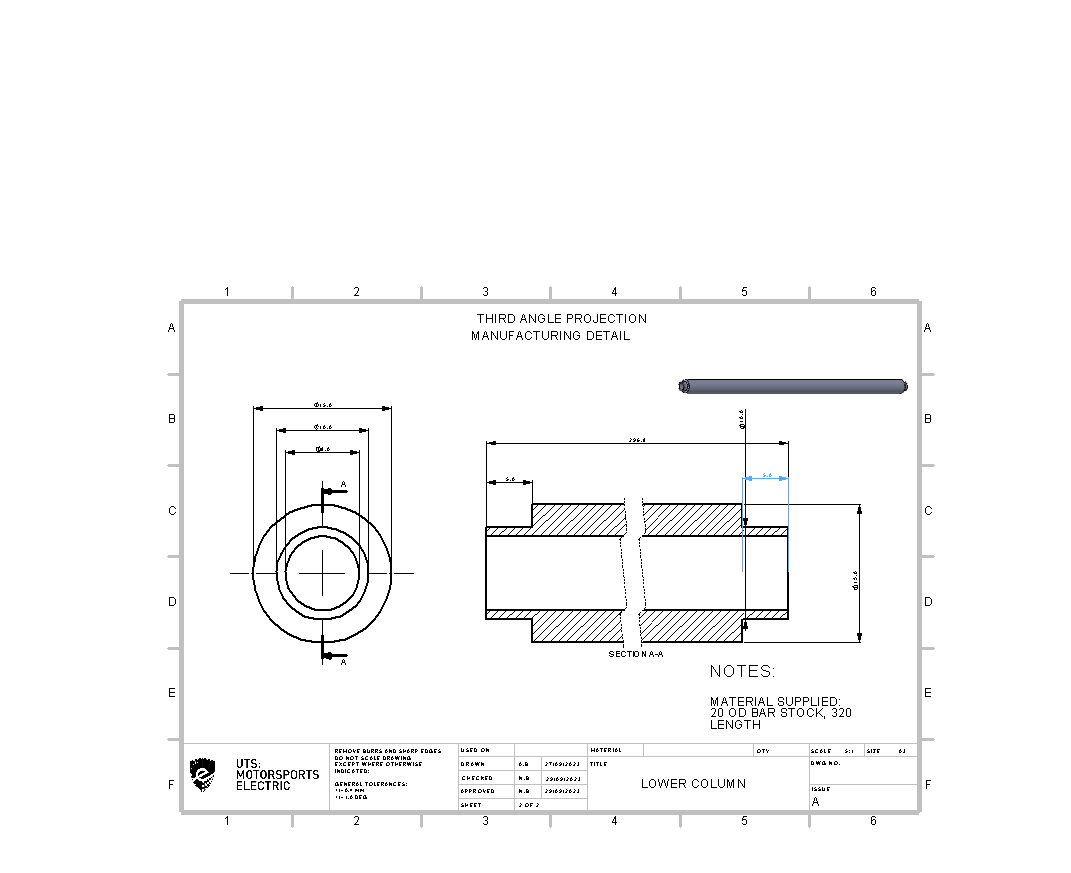
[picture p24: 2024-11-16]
Documentation/Calculations/Steering/Lower Steering Column.JPG

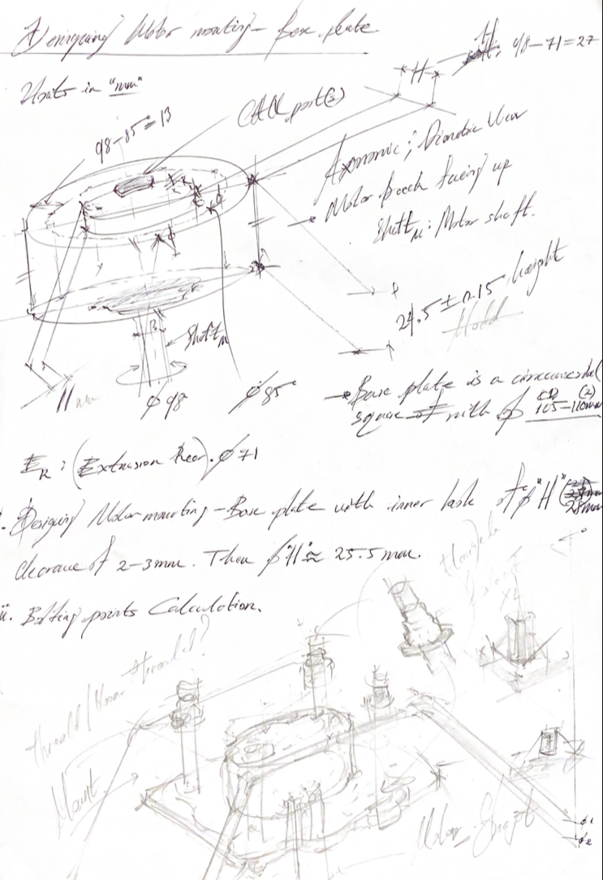
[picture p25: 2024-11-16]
Documentation/Ideation Sketches/Motor Mount/Sketch_v6.jpeg

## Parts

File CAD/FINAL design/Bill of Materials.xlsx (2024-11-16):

Item Number | Part Number | Part Name | Quantity | Material | Specifications | Manufacturer | Vendor | Unit Cost | Total Cost | Manufacturer Link | Vendor Link
1 | AK80-9 | AK80-9 Brushless Motor | 1 | - | Torque: 9 Nm, Max Speed: 437 rpm | CubeMars | Marc Carmichael | $579.90 | $579.90 | https://www.cubemars.com/goods-982-AK80-9.html
2 | NUCLEO-L476 | STM32 NUCLEO-L476RG Microcontroller | 2 | - | ARM Cortex-M4, 80 MHz, 512 KB Flash | STMicroelectronics | Mouser | $23.79 | $47.58 | https://www.st.com/en/evaluation-tools/nucleo-l476rg.html | https://mou.sr/4fNmxub
3 | 5708 | CAN Transceiver | 2 | - | MCP2515 CAN Controller, SN65HVD230 Transceiver | Adafruit | Mouser | $6.20 | $12.40 | https://www.adafruit.com/product/5708 | https://mou.sr/48T7vRf
4 | 204-2980 | Timing Belt, 8 mm Pitch | 1 | Rubber | 8 mm pitch, 30 mm wide, 720 mm length | OPTIBELT | RS Components | $67.47 | $67.47 |  | https://au.rs-online.com/web/p/timing-belts/2042980
5 | P24-8MGT-20 | Sprocket, 24 Tooth, 8 mm Pitch | 1 | Steel | 24 teeth, for 30 mm wide belt | Gates | Biedler's Belts | $99.30 | $99.30 |  | https://www.biedlers-belts.com/gates-p24-8mgt-20-sprocket.html
6 | P72-8MGT-20 | Sprocket, 72 Tooth, 8 mm Pitch | 1 | Steel | 72 teeth, for 30 mm wide belt | Gates | Biedler's Belts | $226.08 | $226.08 |  | https://www.biedlers-belts.com/gates-p72-8mgt-20-sprocket.html
Total |  |  |  |  |  |  |  |  | $1032.73

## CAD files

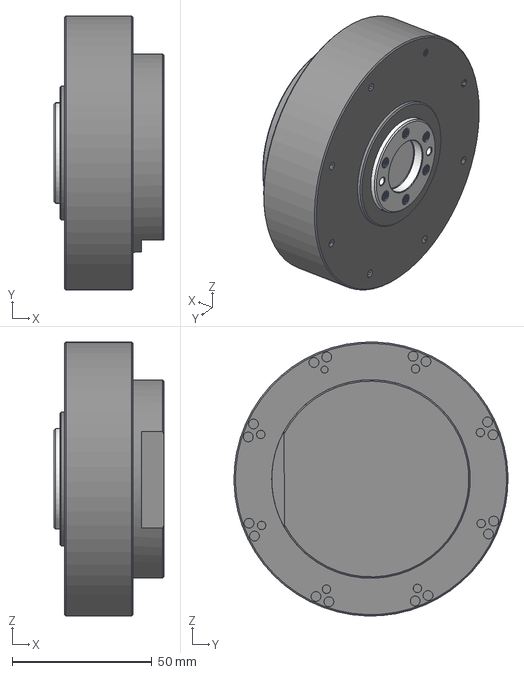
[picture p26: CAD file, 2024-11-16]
CAD/FINAL design/P1/AK80-9/AK80-9_Assembly v2.step
39.2 x 98.0 x 98.0 mm

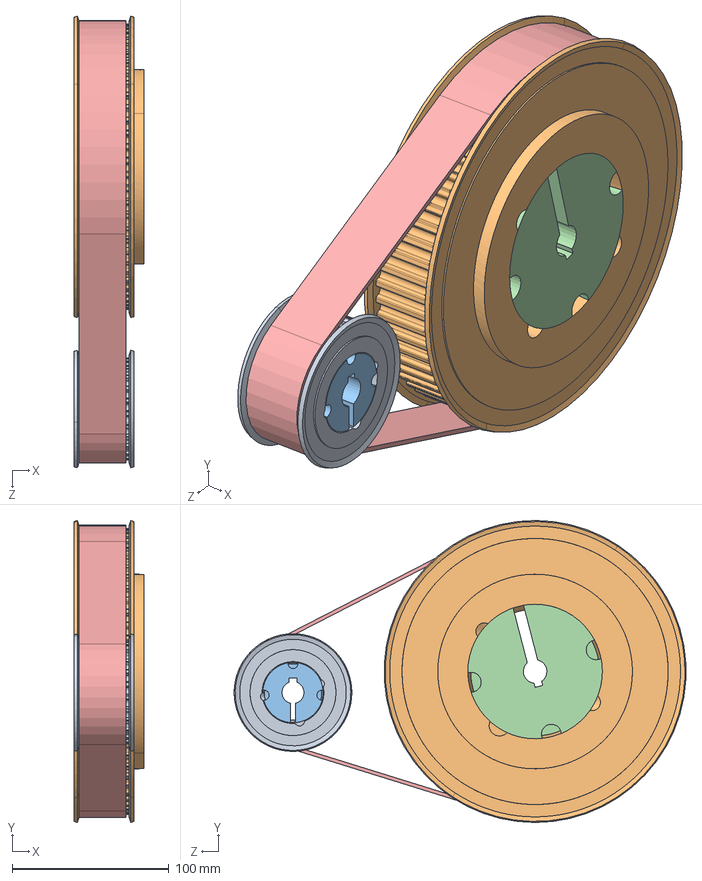
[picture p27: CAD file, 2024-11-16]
Documentation/Calculations/Gears & Pulley/Pulley design and calculations/Belt and pulley assembly (via mate) .SLDASM
44.5 x 192.4 x 287.8 mm
bandbmnfg_26-8p30-1108_
bandbmnfg_72-8p30-2517_
bushing_1108_14
bushing_2517_15
Belt1-16^Belt and pulley assembly (via mate)
Part19^Belt and pulley assembly (via mate)

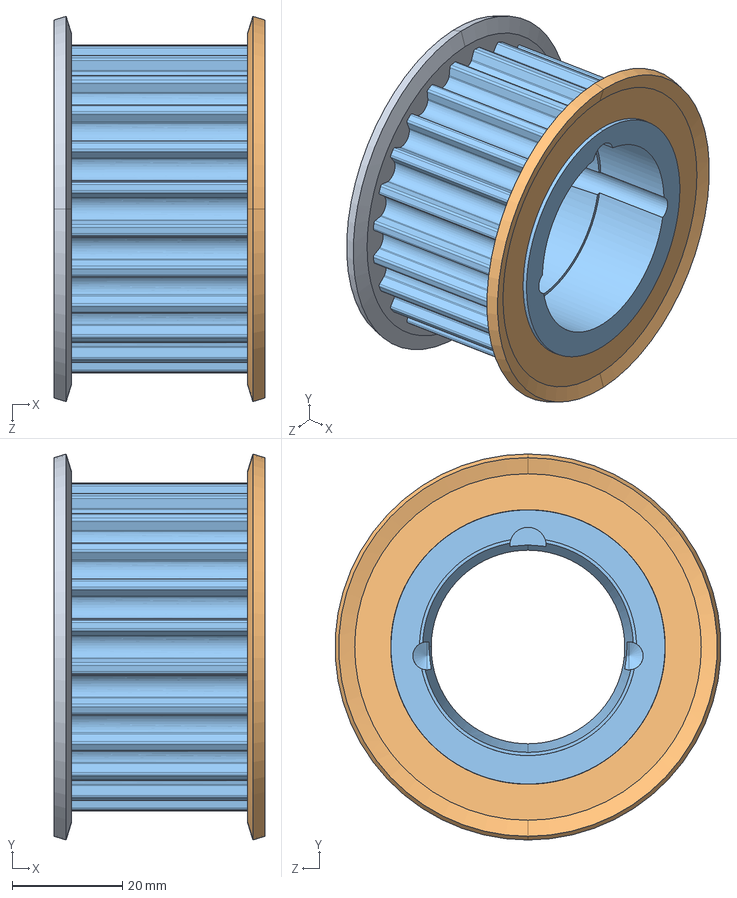
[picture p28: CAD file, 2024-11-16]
Documentation/Calculations/Gears & Pulley/Pulley design and calculations/Solution 2/CAD/24 - 36 - 30mm/bandbmnfg_24-8p30-1108-1/bandbmnfg_24-8p30-1108_.SLDASM
38.2 x 70.0 x 69.9 mm
bandbmnfg_24-8p30-1108__1.prt
bandbmnfg_24-8p30-1108__2.prt
bandbmnfg_24-8p30-1108__3.prt

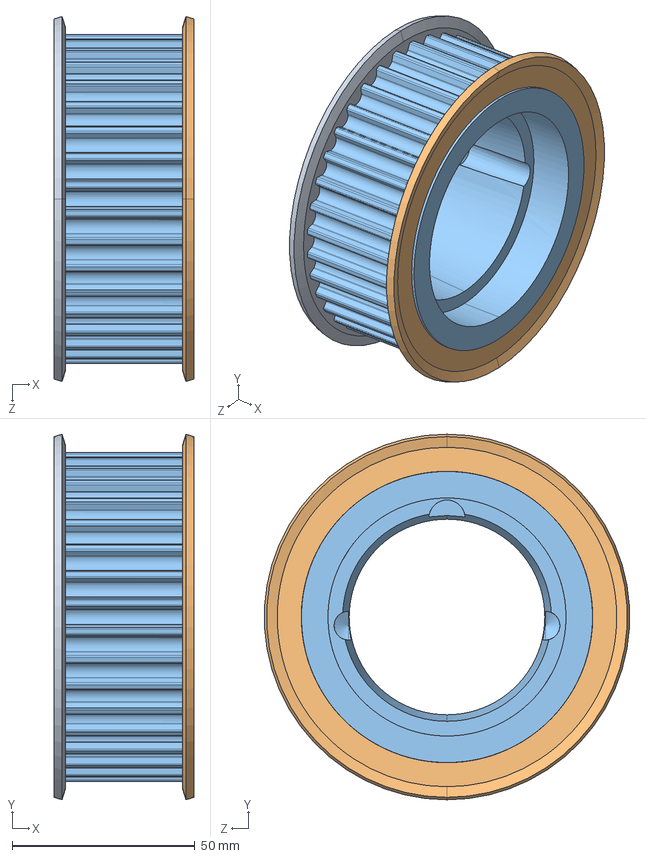
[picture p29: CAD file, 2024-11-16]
Documentation/Calculations/Gears & Pulley/Pulley design and calculations/Solution 2/CAD/24 - 36 - 30mm/bandbmnfg_36-8p30-1610/bandbmnfg_36-8p30-1610_.SLDASM
38.2 x 100.0 x 99.8 mm
bandbmnfg_36-8p30-1610__1.prt
bandbmnfg_36-8p30-1610__2.prt
bandbmnfg_36-8p30-1610__3.prt

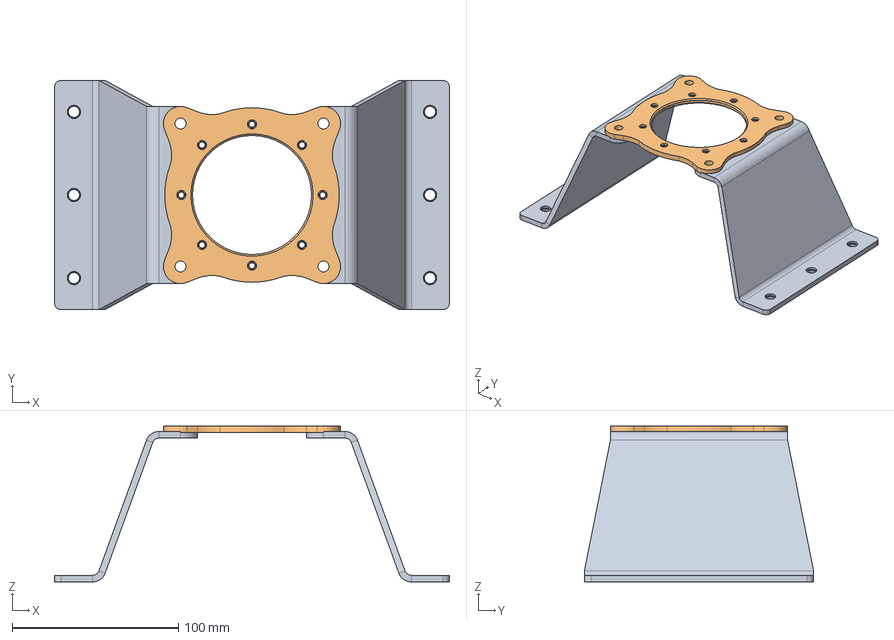
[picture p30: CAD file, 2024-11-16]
CAD/Motor Mount/Mount_Design_Files v1/Assembly1 v8.step
237.6 x 137.8 x 93.7 mm
Save2 v2 Copy
Save2 v2 Copy v5(Mirror)

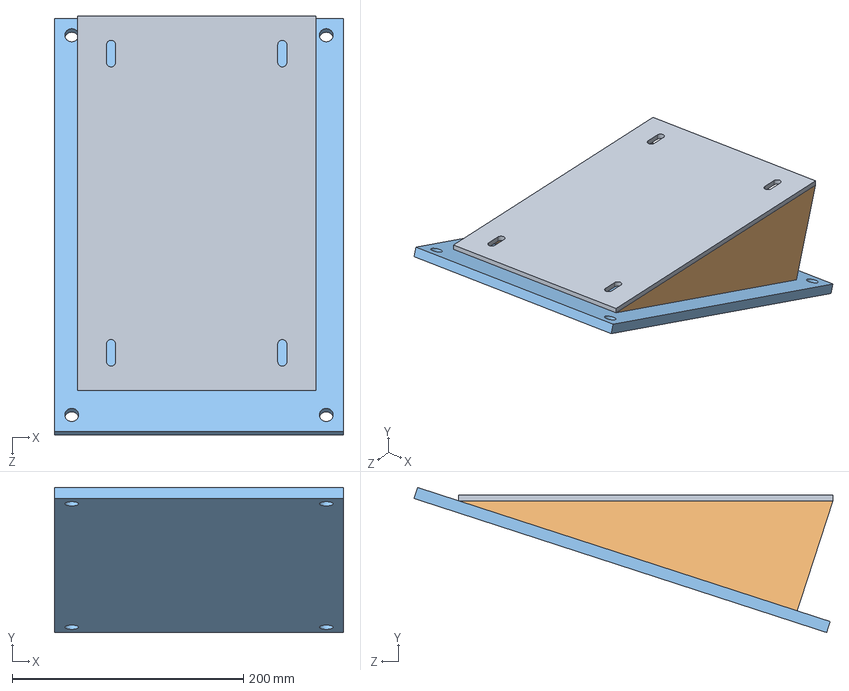
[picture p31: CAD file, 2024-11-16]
CAD/Wedge Model/Wedge Model.SLDASM
250.0 x 125.4 x 362.1 mm
Base Plate Top V1
Side Supports V1 x 3
Base Bottom

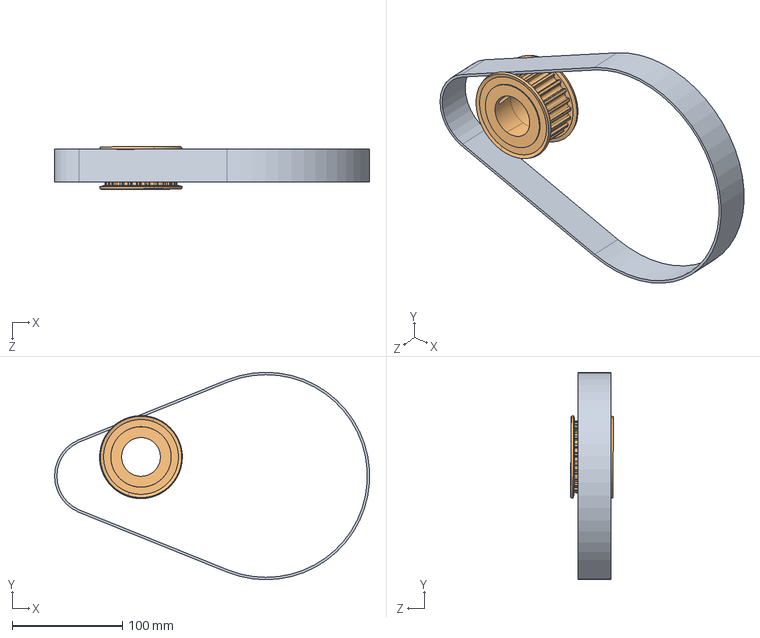
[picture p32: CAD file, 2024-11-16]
Documentation/Calculations/Gears & Pulley/Pulley design and calculations/Belt and pulley assembly.SLDASM
285.4 x 188.0 x 38.9 mm
720 - 8mm - 30mm pulley - Kelvin
bandbmnfg_26-8p30-1108_

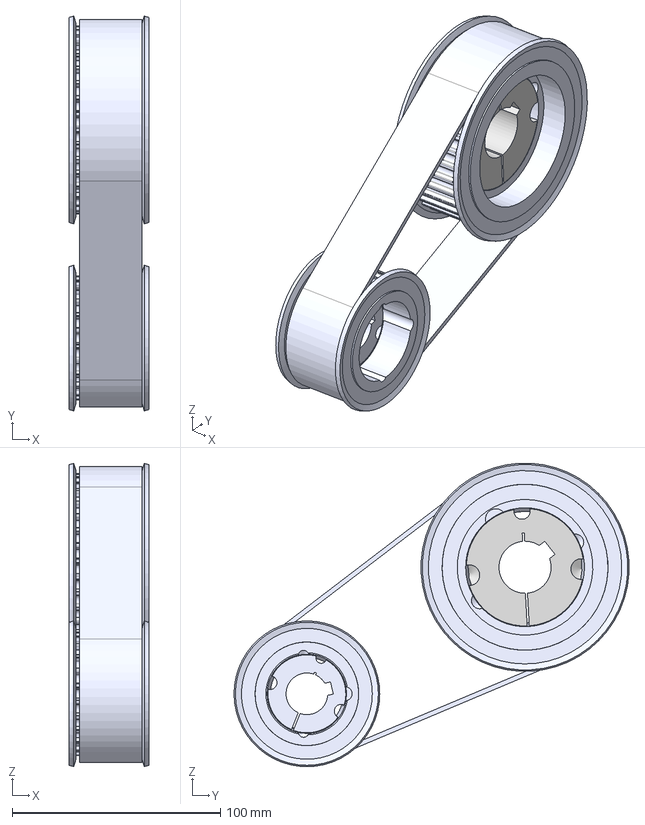
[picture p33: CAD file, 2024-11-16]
CAD/FINAL design/General_Components/Pulley_Assembly.step
38.2 x 189.7 x 145.7 mm
bandbmnfg_24-8p30-1108__1.prt
bandbmnfg_24-8p30-1108__2.prt
bandbmnfg_24-8p30-1108__3.prt
bandbmnfg_36-8p30-1610__1.prt
bandbmnfg_36-8p30-1610__2.prt
bandbmnfg_36-8p30-1610__3.prt
T31074
Belt5-7^Belt and pulley assembly Solution 2

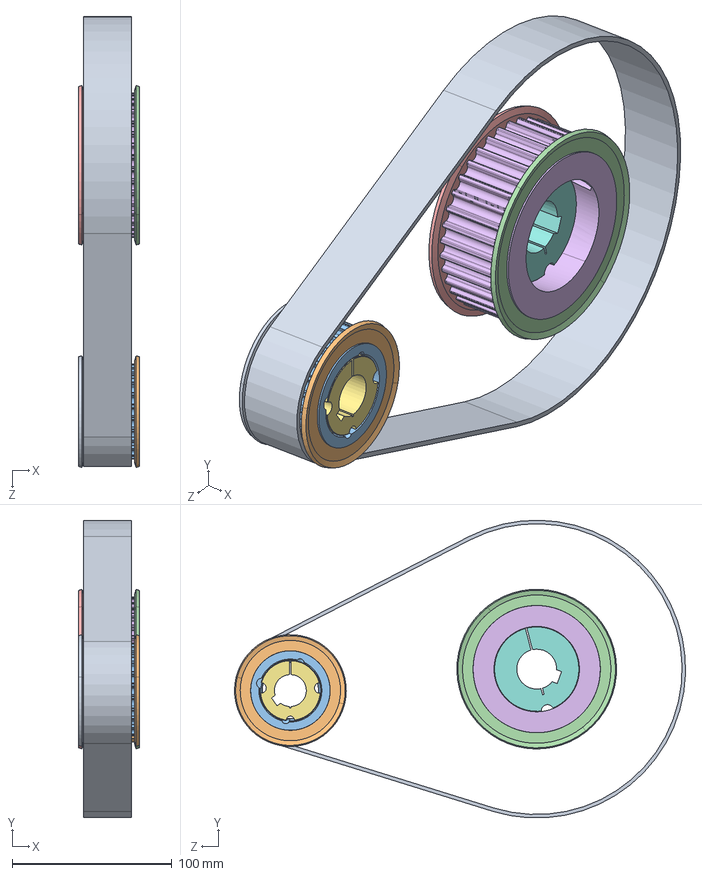
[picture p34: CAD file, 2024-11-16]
Documentation/Calculations/Gears & Pulley/Pulley design and calculations/Solution 2/CAD/Belt and pulley assembly Solution 2 (via mate).SLDASM
38.2 x 186.3 x 282.4 mm
bandbmnfg_24-8p30-1108__1.prt
bandbmnfg_24-8p30-1108__2.prt
bandbmnfg_24-8p30-1108__3.prt
bandbmnfg_36-8p30-1610__1.prt
bandbmnfg_36-8p30-1610__2.prt
bandbmnfg_36-8p30-1610__3.prt
T31074
Belt1-16^Belt and pulley assembly Solution 2 (via mate)
Part19^Belt and pulley assembly Solution 2 (via mate)

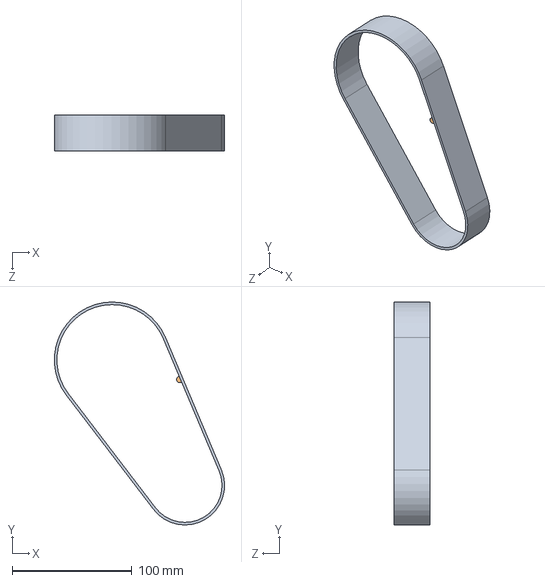
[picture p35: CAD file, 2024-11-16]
Documentation/Calculations/Gears & Pulley/Pulley design and calculations/Solution 2/CAD/480mm 8mm 30mm Belt.SLDASM
142.1 x 186.2 x 30.0 mm
Copy of Belt5-6^480mm 8mm 30mm Belt
8mm single tooth

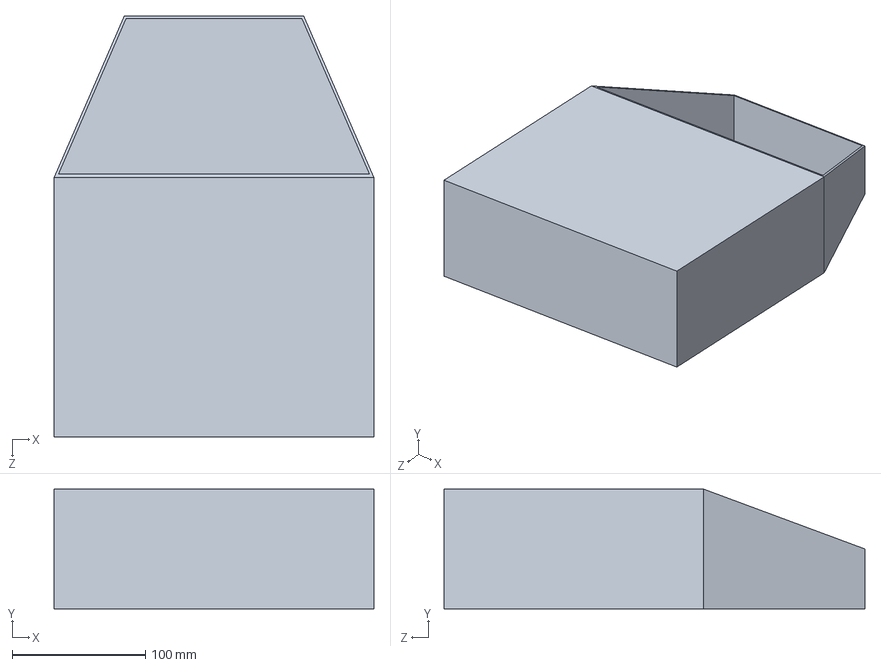
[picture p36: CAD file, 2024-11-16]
CAD/Enclosure/Enclosure.SLDPRT
240.0 x 90.0 x 315.7 mm

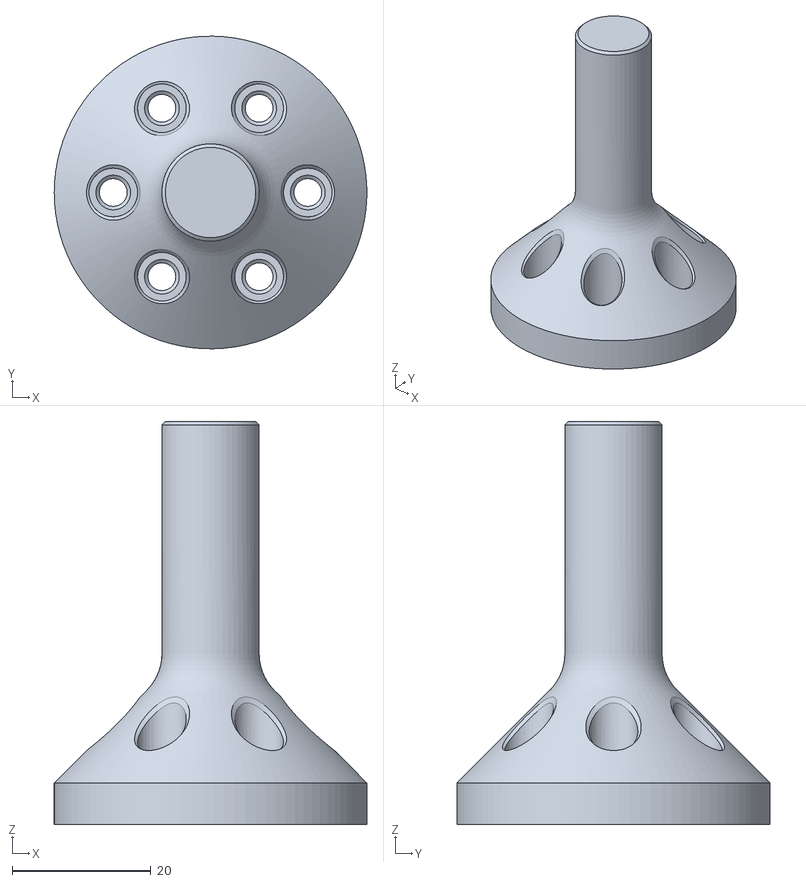
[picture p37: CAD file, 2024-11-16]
CAD/FINAL design/3D_Print_Files/Motor_Shaft v2.stl
45.0 x 45.0 x 58.0

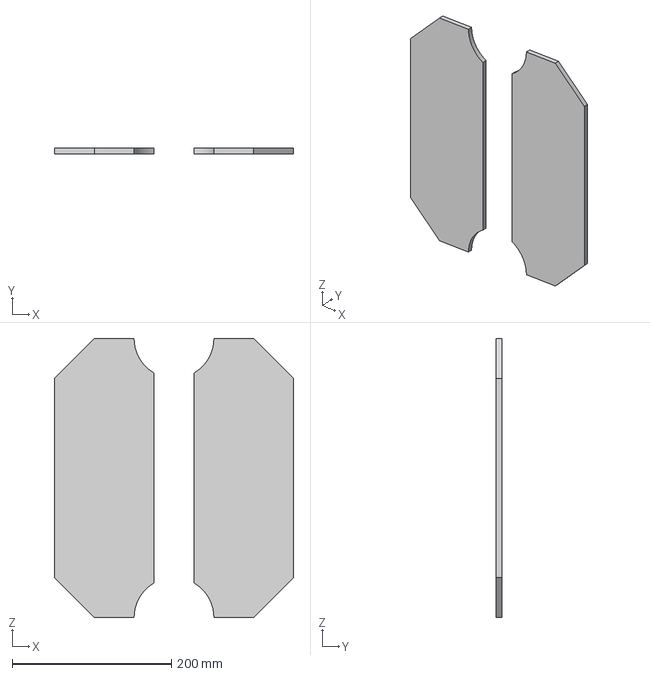
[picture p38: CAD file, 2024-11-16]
CAD/FINAL design/General_Components/Template v1.step
300.0 x 7.00 x 350.0 mm

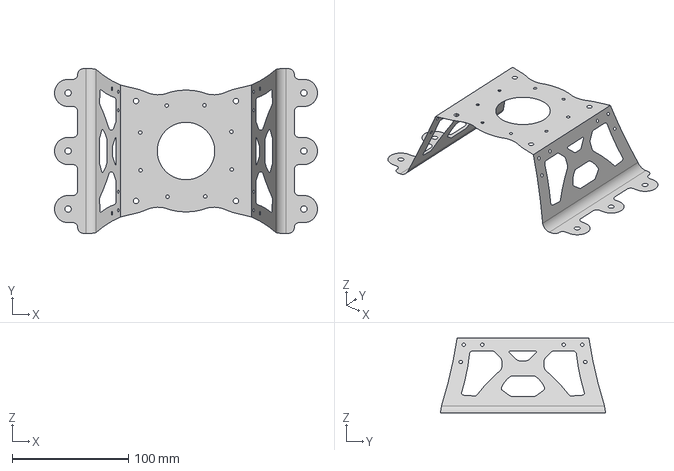
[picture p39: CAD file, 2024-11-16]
CAD/FINAL design/P1/Miscellaneous/Mount_Bracket v2.step
226.5 x 141.8 x 64.2 mm

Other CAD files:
Documentation/Calculations/Gears & Pulley/Pulley design and calculations/Solution 2/CAD/Belt and pulley assembly Solution 2.SLDASM
CAD/FINAL design/P1/Motor_Mount/Mount_Legs v3_Mod v2.step
CAD/FINAL design/P1/UTSME_Autobody_Fitment/Fitment v1.step
CAD/FINAL design/P2/AK10-9/AK10-9_Driving_Flange.step
CAD/FINAL design/3D_Print_Files/Bushing_14 v1.stl
CAD/FINAL design/3D_Print_Files/Motor_Base_Plate_Botm v2.stl
CAD/FINAL design/3D_Print_Files/Motor_Base_Plate_Top v3.stl
CAD/FINAL design/3D_Print_Files/Mounting_Plate v4.stl
CAD/FINAL design/3D_Print_Files/Pulley_Driven v1.stl
CAD/FINAL design/3D_Print_Files/Pulley_Driving v1.stl
CAD/FINAL design/Final Design Drawings/24T Pulley & Bushing/1108TaperBushing.SLDDRW
CAD/FINAL design/Final Design Drawings/24T Pulley & Bushing/24-8p-30 Pulley Drawing.SLDDRW
CAD/FINAL design/Final Design Drawings/24T Pulley & Bushing/Set Screw 0.25in.SLDDRW
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

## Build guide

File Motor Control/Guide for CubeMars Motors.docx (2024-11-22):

# Guide: Interfacing with CubeMars AK Series Motors

# Introduction

This document introduces the control of CubeMars AK series motors using CubeMars software and STM32 microcontrollers. Below is a collection of useful resources, and on the following pages, the hardware setup will be described. This is followed by a quick-start guide to using the CubeMars software and, finally, descriptions of the developed code for STM32 microcontrollers.

# Resources

## CubeMars

AK80-9 specs and graph: https://www.cubemars.com/goods-982-AK80-9.html

AK80-9 specs and graph: https://uav-en.tmotor.com/html/2021/A_0106/640.html

AK Series Q&A: https://www.cubemars.com/article-262-AK+Series.html

AK Series Module Driver User Manual (included in the Motor Control folder): https://www.cubemars.com/images/file/20240611/1718085712815162.pdf

Software and video guides: https://www.cubemars.com/article.php?id=261

Download “CubeMars upper computer” from the last link and follow the first few video guides to connect the motor. If you can’t connect, try installing “CH340 Driver” on your PC. To get the motor running, watch video 2, “MIT mode control”, and make sure you follow all the steps.

## STM32

NUCLEO-L476RG website: https://www.st.com/en/evaluation-tools/nucleo-l476rg.html

For easy access to convenient references, the following files have been collected in the “NUCLEO-L476RG” folder:

- Data brief for Nucleo-64 boards (nucleo-l476rg.pdf)
- User manual for Nucleo-64 boards (um1724-stm32-nucleo64-boards-mb1136-stmicroelectronics.pdf)
- Pinout for NUCLEO-L476RG (NUCLEO-L476RG Pinout.png)
- Screenshot of default pinout configuration (IOC Config Default.png)
- Screenshot of current pinout configuration (IOC Config 2024-10-28.png)
- Datasheet for STM32L476xx microcontrollers (stm32l476rg.pdf)
- Reference manual for STM32L4xxxx microcontrollers (rm0351-stm32l47xxx-stm32l48xxx-stm32l49xxx-and-stm32l4axxx-advanced-armbased-32bit-mcus-stmicroelectronics.pdf)

# Hardware Configuration

## Setup for CubeMars Software Control

To control the motor, the R-LINK is connected to the PC using a USB cable. The R-LINK is then connected to the CAN and Serial ports on the motor using the supplied cable.

The motor should then be connected to a power supply set to 24-48 V (also tested successfully at 18 V). The AK80-9 motor is rated for 12 A and a peak of 24 A, but a significantly lower current limit can be used to be on the safe side.

The setup with the AK80-9 motor and R-LINK is shown in Figure 1.

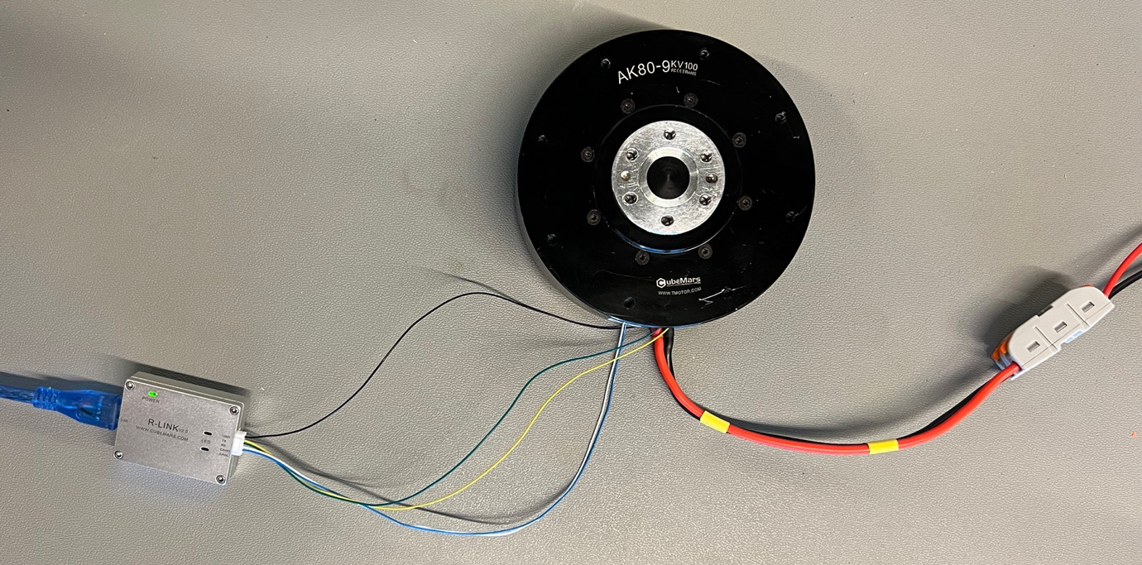
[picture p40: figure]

Figure 1: Setup of motor for test with CubeMars software.

## Setup for STM32 Control

The NUCLEO-L476RG development boards are connected to the PC using USB Mini-B cables. When working with multiple MCUs, it can be helpful only to connect one of them to the PC using a data cable while the other one is just connected to a power source. This avoids confusing the MCUs with each other when debugging.

The current input pinout configuration in the initialisation and configuration (IOC) tool (referred to as STM32CubeMX) is shown in Figure 2. Of main interest are the CAN RX and TX (upper left) and the Potentiometer (left).

The physical pinout of the Nucleo development board is shown in Figure 3.

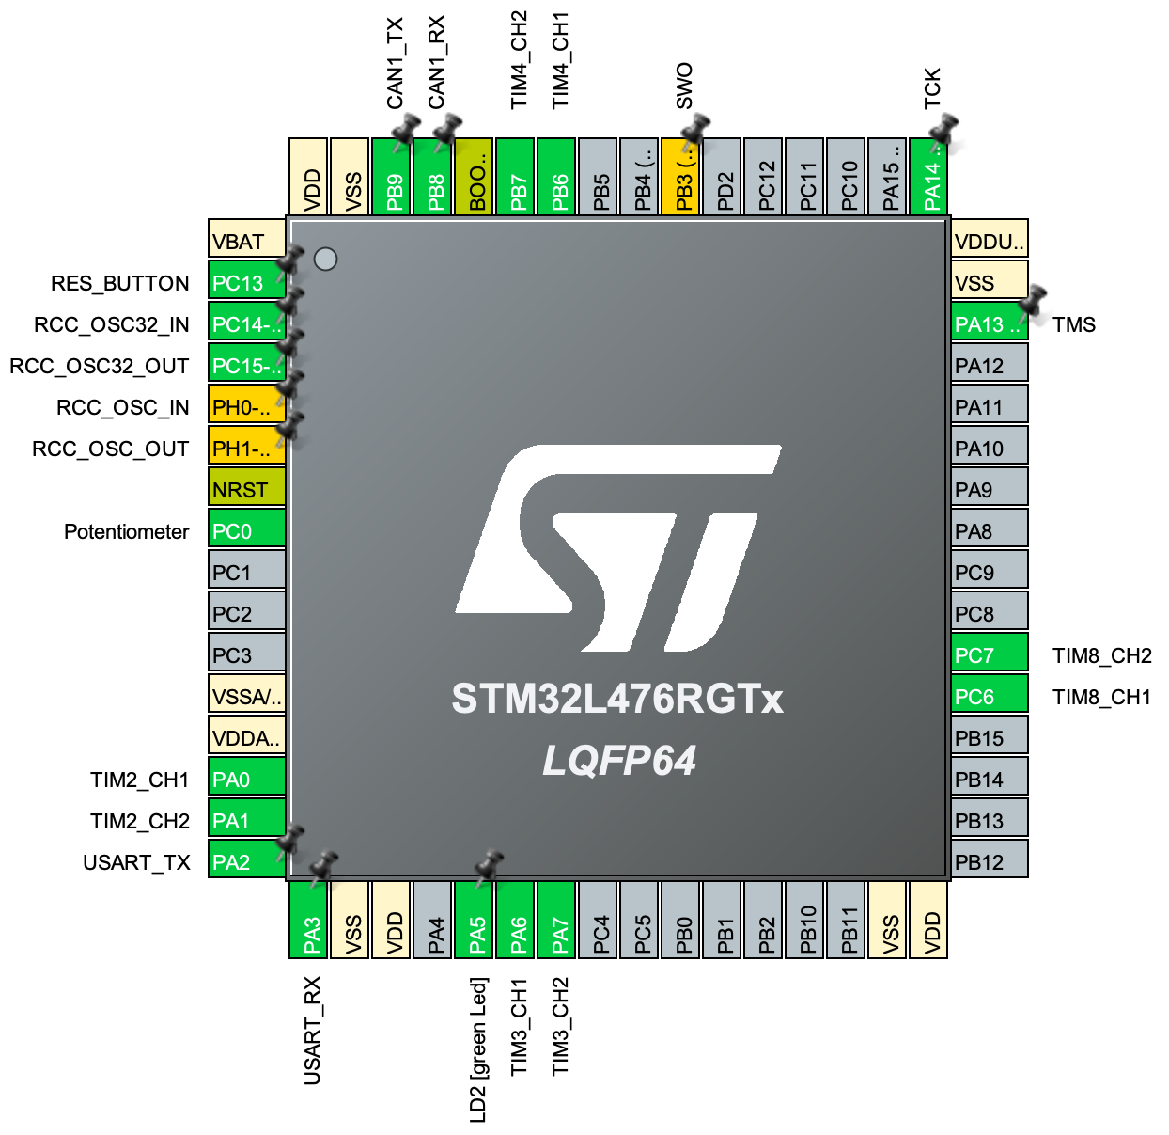
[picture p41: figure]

Figure 2: IOC pinout configuration viewed in STM32CubeIDE.

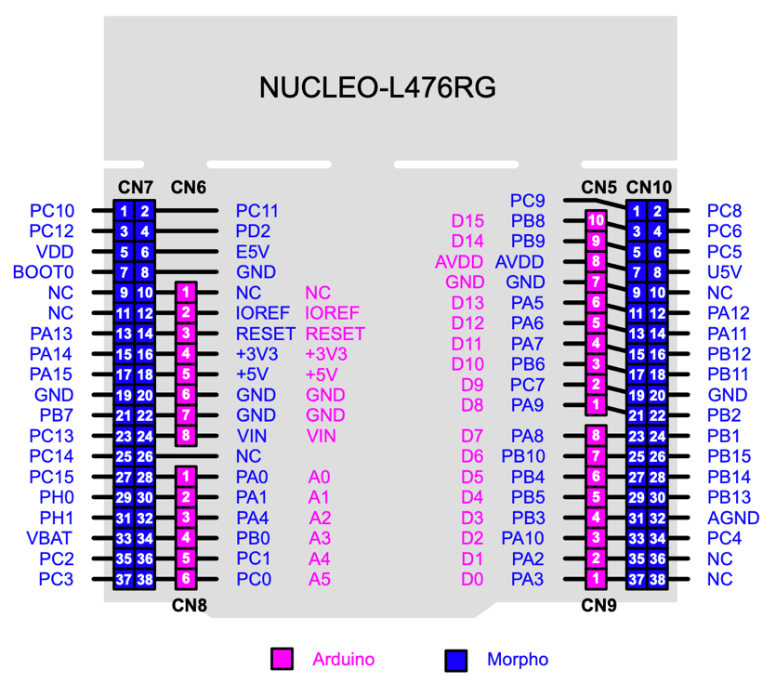
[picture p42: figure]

Figure 3: Physical pinout of NUCLEO-L476RG.

Referring to the physical pinout, the connections to be made on the board are:

1. CAN transceiver Vcc: +5V (left)
2. CAN transceiver GND: GND (left)
3. CAN transceiver RX: PB8/D15 (upper right)
4. CAN transceiver TX: PB9/D14 (upper right)
5. Potentiometer Vcc (purple): +3V3 (left)
6. Potentiometer GND (grey): GND (left)
7. Potentiometer Signal (yellow): PC0/A5 (lower left)

To facilitate communication between two or more units, they should be connected CANH-CANH (blue-blue) and CANL-CANL (white-white). The setup for communication between two Nucleo boards is shown in Figure 4. The setup for testing motor control from a Nucleo board is shown in Figure 5.

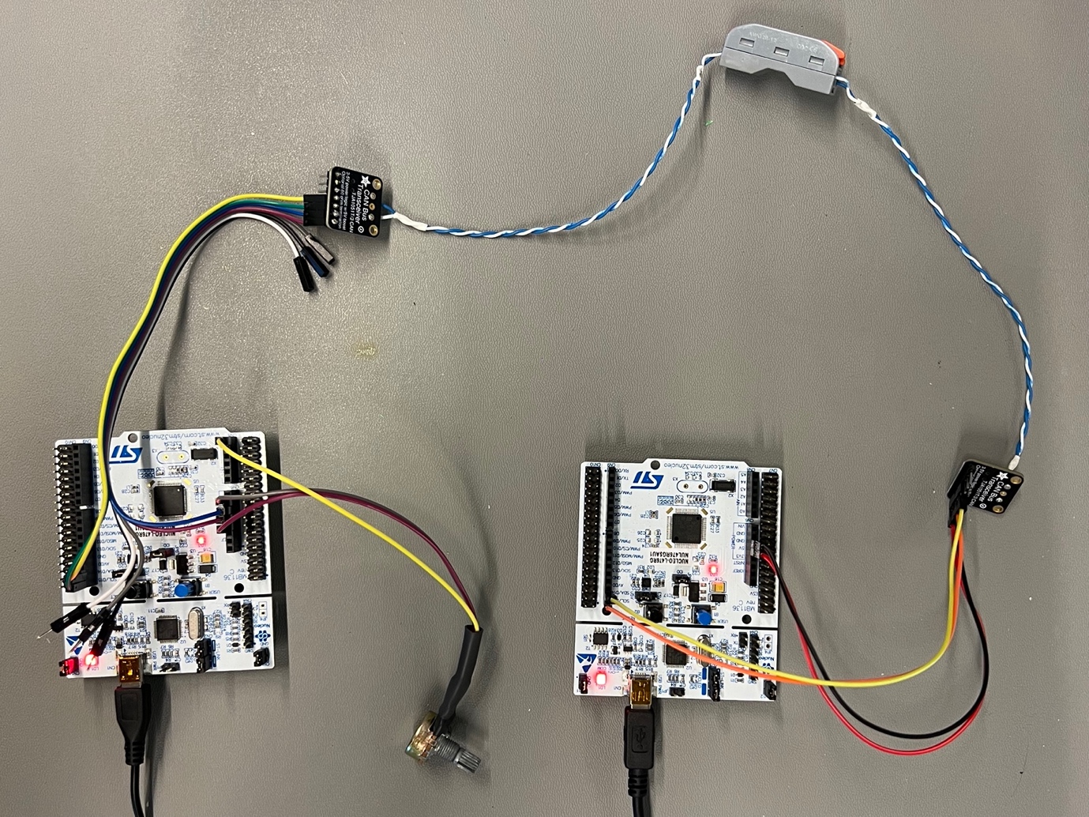
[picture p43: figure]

Figure 4: Setup of Nucleo boards for test of CAN communication.

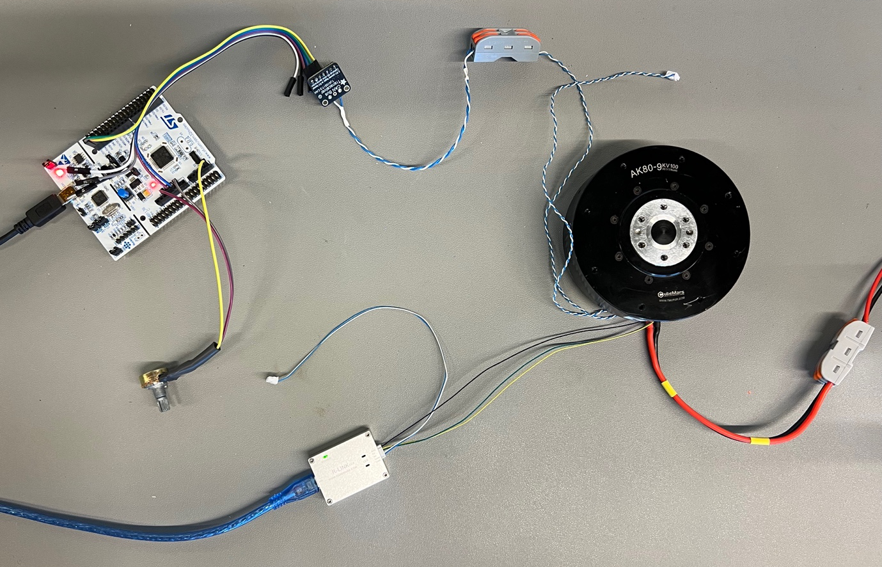
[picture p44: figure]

Figure 5: Setup of Nucleo board and motor for test of motor control.

# CubeMars Software

The CubeMars software (referred to as the “upper computer”) can be downloaded from the link under Resources above. A screenshot of the software is shown below.

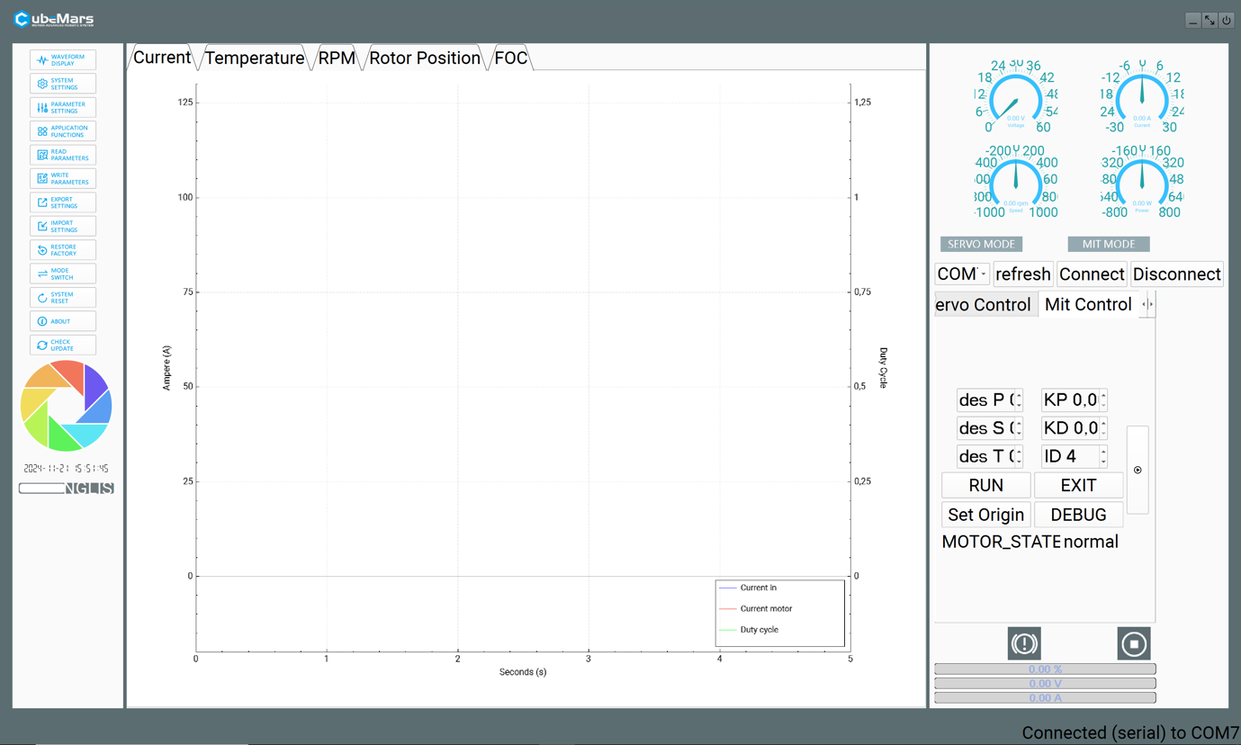
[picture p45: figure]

## General Usage

The software is a bit quirky and will likely take some getting used to. Start by maximising the window and changing the language to English using the switch below the colourful circle on the left.

Most controls are done in the panel on the right. To connect the motor, start by pressing “refresh”. This should display the relevant COM port in the dropdown, which can then be connected by pressing the “Connect” button. The status in the lower right corner should then change accordingly.

Two built-in control modes exist, “Servo Control” and “MIT Control”. Both can be used for position and/or speed control, but the difference lies in the control structure (refer to the user manual for block diagrams). In this guide, MIT mode will be used.

To control the motor in MIT mode, select the “Mit Control” tab on the right. First, set the motor’s CAN ID. (If you don’t know the motor’s CAN ID, see Debug Panel below.) Make sure all other values are zero. Then, press “RUN” to start continuous CAN communication with the motor. At this point, you should see the graphs in the centre starting to display real-time data received via CAN. Press “Set Origin” to ensure the motor’s current position is zero before starting position control (forgetting this step can result in sudden, unexpected movement). Set the Kp (position control) and Kd (speed control) parameters and the position (“P”) and speed (“S”) setpoints. Press the vertical play button to send the command, and the motor should move accordingly. You will need to press the play button every time you want to send a command with new parameters. In the centre, switch between tabs to see waveforms of position speed, temperature, duty cycle, DC current, FOC currents, etc. To stop control, press “EXIT”.

The above procedure is also shown in the video on GitHub.

As a conservative starting point, Kp = 0.5, Kd = 0.2 and S = 0 can be used for position control. In this case, Kp controls the position to the P reference, and Kd limits the speed. For pure speed control, Kp = 0 and Kd = 0.2 can be used. In this case, the P reference has no effect, and Kd controls the speed to the S reference.

Additionally, it is possible to command a feed-forward torque (“T”), which translates directly to a current without any associated feedback control.

## Debug Panel

When the serial connection has been established (through the COM port, as described above), the motor can be controlled using a CAN connection (though the CAN ID). If the CAN ID is unknown, it can be found through the Debug panel. This panel can also be used to read or set other parameters, to monitor encoder data and other things.

To see the configuration of the connected motor, first go to the debug panel by pressing the “DEBUG” button in the “Mit Control” tab on the right. This opens a command line-like interface for serial communication.

To read motor parameters, enter “setup”. This outputs a list of parameters, including the CAN ID. To return to the main debug menu, enter “exit”. Other usable commands are displayed in the main debug menu.

## For More Information

In the left panel, graphical menus not covered in this guide can be opened, such as for settings, system parameters and exporting and importing settings. The “Mode Switch” menu can be used to switch between MIT mode and Servo mode.

For more information about using the CubeMars software, I recommend watching the video guides linked under Resources and referring to the user manual for detailed information about control modes and communication.

# STM32

The code developed for the NUCLEO-L476RG is based on template code from UTS Motorsports. Minimal changes have been made to the existing code and no changes to the IOC configuration. This section will describe the additions to the code in general terms. For details, see the comments in the code.

Most additions have been made in the files cubemars_control.c and cubemars_control.h, which are included in the main file. Many of the functions are based on examples from the CubeMars AK Series User Manual

## Float support for printf

For debugging purposes, printf is used to print values via USB to a serial monitor on your PC. Floating-point support for printf has been enabled to allow the display of floating-point numbers. However, enabling this feature can consume significant flash memory, RAM, and CPU resources, which may negatively impact performance in critical real-time operations.

Recommendation: Before conducting critical testing, you should strongly consider disabling floating-point support and generally limiting or eliminating the use of printf to minimise resource usage.

To enable floating-point support in STM32CubeIDE, the flag “-u _printf_float” was added under Project Properties > C/C++ Build > Settings > Tool Settings > MCU GCC Linker > Miscellaneous > Other flags. To disable floating-point support, simply remove this flag.

## Constants and typedefs in cubemars_control.h

In addition to function prototypes, cubemars_control.h declares four special CAN commands used for entering and exiting motor control mode, setting the origin and reading the state (note that the command for reading the state is identical to the command for entering motor control mode). The function also declares limits for position, velocity, torque and control parameters. The values of the constants are assigned in cubemars_control.c.

Additionally, a typedef for an enumeration (enum) defining different error codes received from the motor, which can be useful for monitoring.

## Functions in cubemars_control.c

In cubemars_control.c, values are assigned to the special CAN commands and limits mentioned above. Additionally, it contains functions used for communication with sending commands to CubeMars motors and receiving feedback. Most of these functions are based on examples from the user manual, many of them with modifications.

# Conclusion

The motor can be successfully controlled using CubeMars software when connected to a PC using the R-LINK. The communication between the microcontrollers via the CAN transceivers also seems to work as expected. However, trying to send commands to the motor did not work, which could suggest that the current CAN configuration on microcontrollers could be incompatible with the motor.

## Recommendations for Future Work

Using the setup in Hardware Configuration and following the guide in CubeMars Software should allow for quickly getting the motor running using a PC connection.

The code described in STM32 provides a foundation for further testing and the development of an API for controlling CubeMars AK motors using STM32 microcontrollers, following adjustments to make the CAN communication compatible.

43019 DMMS T21 - P29 - Autonomous Steering Mechanism 22 Nov 2024

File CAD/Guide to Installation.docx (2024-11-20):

Guide: Installing Autonomous Steering Mechanism with Vehicle

# Resources

## Main Parts

- AK 80-9 Motor
- Motor Mount
- Motor Wedge
- Gears
- Belt
- Enclosure

## Other Tools

- Specify Nuts & Bolts
- Specify tools such as wrench, drills etc.
- Motor Mounting Plates

May need the assistance of experienced FEIT lab personnel.

# Installation

## Motor Mount

- Specify Installation for mount

## Motor

- Specify Installation for motor and plates

## Wedge

- Specify Installation for wedge

## Belt & Gears

- Specify Installation for gears

## How to Adjust Belt

- With relation to wedge

## Issues that may occur

- Stuff that could go wrong with motor and gears etc.

# Recommendations for Space Constraints

Where to place holes (Insert CAD screenshot) in floor of car

Suggestion to use a different motor AK10-9

Using a different gear ratio

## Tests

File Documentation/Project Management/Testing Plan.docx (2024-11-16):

# Testing & Validation Plan

# Introduction

This document details the testing needed to confirm that the product lives up to the evaluation criteria in the agreed upon project specification (amended in this document).

First, the revised design objectives and evaluation criteria will be stated, with a summary of how the objectives have been met. On the following pages, the testing procedure for each design objective will be described.

# Design Objectives & Evaluation Criteria

Design Objective | Evaluation Criteria | How was it achieved?
Mechanical Strength | Materials used must be in accordance with FSAE rules. | FEA, calcs, minimum components and p.o.f.
Ease of Manufacture | How well the system uses the minimal number of parts, and assembly complexity, thereby increasing efficiency, accuracy, and overall product quality and reliability. | Sheet metal design that can be cut and bend into shape.
Lightweight | Must fit under the vehicular mass limit of 300kg. (Attempt to keep it as light as possible without sacrificing mechanical integrity.) | Weight is not unreasonably large (insignificant according to UTSMA).
Modular | Must be able to dismount and remount it onto different vehicles (iterations) without damaging the components. | Only the angle of wedge needs to be redesigned.
Disengageable | The autonomous steering system must be designed for easy disengagement, allowing manual control of the car via the steering wheel. | Motor is backdrivable.
Ergonomic | Must allow template from FSAE to pass through. | Template from FSAE can pass through CAD assembly.
Safety | “T.1.3.3 All moving suspension and steering components and other sharp edges inside the cockpit between the front hoop and a vertical plane 100 mm rearward of the pedals, must be shielded with solid material. […] T.1.3.4 Covers over suspension and steering components must be removable to allow inspection of the mounting points.” – Formula SAE Rules 2024 | Casing around moving components.
Control | Must be able to track position and velocity references within sufficient accuracy (of 6 degrees). | Motor can be controlled using CubeMars software.
Interfacing | Consistently receiving command from central controller, measure steering position and transmitting it to central controller. | Inter-connected STM32 microcontrollers can communicate internally and with motor.

# 1 Mechanical Strength

## Materials

- PC with following software:
  - Ansys
  - Fusion 360
  - SolidWorks
  - Excel

## Testing Procedure

Step | Testing Specification
1 | Extract the latest model of the motor mount via shared files on Teams.
2 | Start-up Fusion and open the target motor mount model on the design workspace
3 | Navigate and switch from design to simulation workspace.

# Simulation setup:

- Select the simulation material (Used materials: Mild steel & Aluminium in accordance to FSAE rules)

# Apply constraints to the motor mount by selecting the inner mounting holes on the base of the motor mount and constraint them to remain static in all available axes

# Apply a scaled-up vertical load of 10N (mass of the motor is 4N).

- Apply a lateral load of 1.25 times the maximum torque of the Cube Mars BLDC (available in Cube Mars AK80 – 9 data sheet)
- Generate automatic contacts via simulation settings dock.
- Ensure all bodies are rigid using the “DOF View” under the display in the simulation settings dock.
- Generate mesh and adjust the mesh to be SCALED PER PART.
- Adjust remaining mesh generation parameters accordingly.
- Set a safety factor of 1.5 or above.

4 | Running the simulation - Run (“Solve”) the simulation. - Once the simulation ends, refer to the safety factor and review whether the structure is able to withstand the loads after the application of the safety factor. - Check simulation progress via “Job Status” icon in the dock. - For a deeper analysis, activate modes such as Stress, displacement or strain to clearly review the affected regions of the motor mount as a result of these load applications.
| Simulation results: - Given the simulation results, review the legend to observe the degree at which the loads cause the motor shaft to experience loads. (i.e.; Stress: Red for high-stress, Blue for low-stress)
5 | Verifying and cross-checking all calculations and FEA results and hand calculations. - Upon activating “Simulation Results”, visit the “INSPECT” tab in the dock and select point probes of choosing - Create the point probe and apply them at the desirable regions to extract the relevant information with preferred units.

# 2 Lightweight

Must remain within the 300kg vehicular mass limit. Aim to keep the weight as low as possible without compromising mechanical integrity. The weight should not be excessively large, along with the system not be over-engineered design consisting of heavier components.

## Materials

- SolidWorks files
- Manual calculations

## Validation Procedure

Step | Testing Specification
1 | Ensure that the calculations and computer simulations of the parts are not over-engineering.
2 | Verify components after manufacturing to ensure that components match up with their designed weight with weight scale.

## Results

By applying a factor of safety between 1.5 and 3 for various components, the parts are designed efficiently without being over-engineered. This approach avoids unnecessary and excessive material use in terms of thickness, width, to avoid unnecessary weight.

# 3 Ease of Manufacture

The ability to design the system with the goal of minimising the number of components in the assembly. The manufacturing process should be as efficient as possible to reduce unwanted complexities and cost.

## Materials

- SolidWorks files
- Manufacturing procedure guidelines
- Manual calculations

## Validation Procedure

Step | Testing Specification
1 | Ensure that the calculations and computer simulations of the parts are not over-engineering.
2 | Ensure that design of the components have ease of manufacturability as an intent (i.e. do not design parts which are hard to manufacture).
3 | Ensure that the manufacturing process is a streamlined as possible.
4 | Create manufacturing guidelines to ensure ease of manufacture and quality control.

## Results

Using a factor of safety between 1.5-3 for various components, this results in the parts themselves to not be over-designed and have unnecessary and additional material components in terms of thickness, width, etc.

# 4 Modular

Ability to integrate the module in a variety of steering setups which would be present each UTSM car, over the years.

To alter the module to fit in future car variants, the angle of the wedge would need to change in accordance with the new angle of the steering shaft. This would bring the Motor mount to the correct orientation to fit with the new steering shaft.

## Materials

- PC with SolidWorks
- SolidWorks file of wedge plate
- SolidWorks file of current Motorsports car

## Validation Procedure

Step | Testing Specification
1 | Open SolidWorks file of current Motorsports car.
2 | Use Evaluate tool to find angle of steering shaft to the floor.
3 | Open SolidWorks file of Wedge Plate.
4 | Alter Angle of incline to match angle of steering shaft.

## Results

In case of major design change, this may not work, and certain aspects of the motor mount design may have to be changed as well for it to be compatible with the new machine. Some of the factors that could be altered include:

- The height of the mount: Depending on the type of belt used to connect with the shaft, it can be brought lower down or higher up, if it is compliant with the FSAE template.
- The design of the side supports to enhance the stability of the motor.
- Inclusion of more or fewer bolts to secure the motor.
- Placing the motor on top of the mount or underneath.

# 5 Disengageable

To enable the system to be disengaged and thus allow manual driving, it was chosen to use a backdrivable motor which can be electrically disconnected. If the system significantly resists the force by the driver, it will impede the drivability of the vehicle.

## Materials

- Datasheet for the motor
- Selection/design of connecting mechanism

## Validation Procedure

Step | Testing Specification
1 | Open the motor datasheet.
2 | Find the backdrive torque.
3 | Is the backdrive torque much lower than the expected steering torque?
4 | Check if connecting mechanism is backdrivable.

## Results

It is found in the datasheet that the rated backdrive torque is 0.51Nm, which is about 40 times lower than the maximum expected steering torque. The motor is connected to the steering column using a belt drive, which is backdrivable with negligible resistance.

# 6 Ergonomics

This is to ensure if the prevailing (to-be proposed) design of the Motor Mount assembly occupies space within the driver cockpit while obeying the constraints inflicted by the driver template, and with aims of passing driver template inspections.

## Materials

- PC with SolidWorks
- SolidWorks assembly
- Driver template model

## Validation Procedure

Step | Testing Specification
1 | Locate the regions of the template that is to be affected (Refer to FSAE Rules Section T1.1 & T1.2).
2 | Consult the dimensions of the template via 2024 FSAE rulebook.
3 | Extract the latest model for the motor mount on the shared folder in week 10. Model name: Motor_Mount v2_Mod.
4 | Finding the X component (max length) via Fusion:
| - Obtain the TOP or BOTTOM view of the motor mount. - Activate the measuring tool. - Measure the distance between each one of the mounting hole pairs on the mounting base of the mount.
5 | Extract the latest model for the motor mount assembly on the shared folder in week 1 Model name: Assembly v4 for step 6.
6 | Finding the Y component (max length) via Fusion:
| - Obtain the FRONT or the BACK view of this assembly. - Activate the measuring tool. - Measure the distance between; i. A vertice that belongs to the top face of the motor. ii. A vertice that belongs to the bottom mounting face of the motor mount. - To find the max vertical height of the module (assembly): i. Activate the “Component 1 co-ordinate system” under the results tab of window that belongs to the measuring tool.
7 | Evaluate whether the assembly obeys the constraints.
| Compare the X and Y components of the assembly and review whether these dimensions satisfy the space available for the template to pass through in the cockpit.

## Materials

- Software; Autodesk Fusion
- Test components; CAD Models via shared folders.
- Measuring tools; Fusion measuring tools.
- Instruments; Calculator (opt.)

# 7 Safety

To comply with the 2024 FSAE rules:

The rotating part of the Motor(s) must be contained in a structural casing. • Minimum thickness for aluminium alloy 6061-T6: 3.0 mm • Minimum thickness for steel: 2.0 mm

The motor casing may be the original motor casing, a team-built motor casing or the original casing with additional material added to achieve the minimum required thickness.

If lower grade aluminium alloy is used, then the material must be thicker to provide an equivalent strength.

## Materials

- A rod
- Model of casing to identify any points of failure
- Micrometre

## Validation Procedure

Step | Testing Specification
1 | Ensure that steering components and its materials are designed to withstand track conditions.
2 | Ensure all components are all are firmly attached to avoid any dislodgement during operation.
3 | Use micrometre on most thin region and check thickness. Ensure it is within the acceptable thickness for the material used.
4 | No sharp structures with could cause bodily injury should extend into the cockpit area in a manner that could hinder the driver’s control of the vehicle or create a safety hazard during a crash

# 8 Control

The motor must quickly and accurately respond to changes in the given position and/or velocity references.

## Materials

- Laboratory power supply (24-48V, 3-24A)
- AK80-9 motor
- CAN+Serial cable
- R-LINK module
- USB cable
- Windows PC with CubeMars software

## Validation Procedure

Step | Testing Specification
1 | Connect the USB cable from the computer to the R-LINK module.
2 | Connect the CAN+Serial cable from the R-LINK module to the CAN and Serial ports on the AK80-9 motor.
3 | Connect the AK80-9 motor to the power supply.
4 | Following the given instructions, setup the software to control the motor.
5 | Check that the motor responds to commands. Use the internal and/or external sensors to measure position and speed.

## Results

The motor can be controlled in speed mode and in position mode. In both modes, the motor responds promptly. The measured angle change in position mode corresponds with the expected angle change, given the reference.

# 9 Interfacing

The microcontrollers must be able to communicate with the central vehicle controller via CAN bus to receive commands and return feedback, and with the motor to control its position and velocity.

## Materials

- STM32 NUCLEO-L476RG microcontroller development boards
- CAN transceivers
- Jumper wires
- Laboratory power supply (24-48V, 3-24A)
- AK80-9 motor
- CAN+Serial cable
- R-LINK module
- USB cables
- PC with STM32CubeIDE software

## Validation Procedure

Step | Testing Specification
1 | Connect the microcontrollers and CAN transceivers (refer to given documentation).
2 | Connect both microcontrollers to a 5V power source, such as the PC, using the USB cable.
3 | Test that the microcontrollers can send messages to each other. This can be done by pressing the blue button on either microcontroller and observing that the LED lights up on the other microcontroller. It can also be done by observing the received data in the debugger on the PC.
4 | Connect the CAN cable from the AK80-9 CAN port to the CAN transceiver’s CAN lines.
5 | Connect the AK80-9 motor to the power supply.
6 | Following the given instructions, use the software to send commands to the motor.
7 | Check that the motor responds to commands. Use the internal and/or external sensors to measure position and speed.

## Results

The microcontrollers communicate successfully with each other (Steps 1-3). Further testing of communication with the motor is required (Steps 4-7).

43019 DMMS T21 - P29 - Autonomous Steering Mechanism 15 Nov 2024

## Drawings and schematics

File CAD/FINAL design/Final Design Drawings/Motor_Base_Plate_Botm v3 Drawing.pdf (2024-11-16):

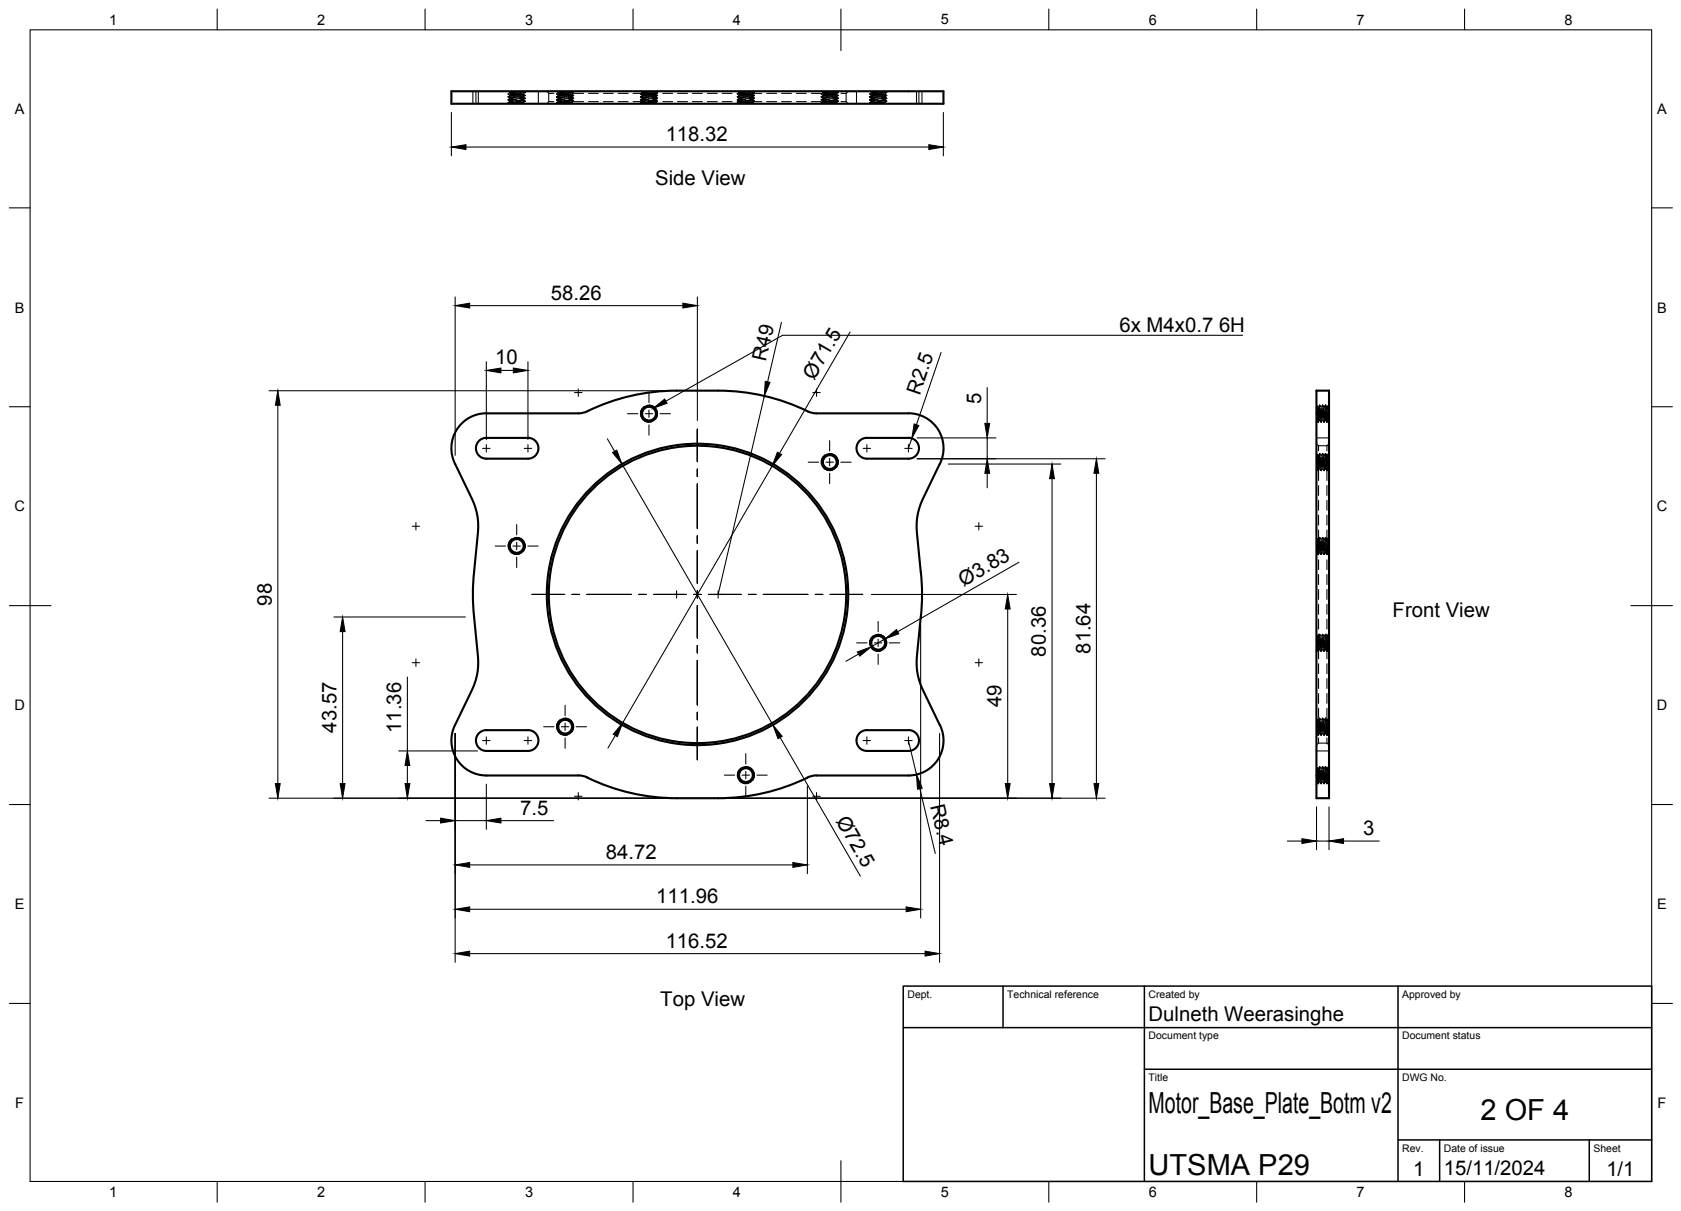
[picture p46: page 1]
Title; DWG No.; Rev.; Date of issue; Sheet; UTSMA P29; Motor_Base_Plate_Botm v2; Top View; Side View; Front View

Dept. | Technical reference | Created by Dulneth Weerasinghe | Approved by

Document type | Document status

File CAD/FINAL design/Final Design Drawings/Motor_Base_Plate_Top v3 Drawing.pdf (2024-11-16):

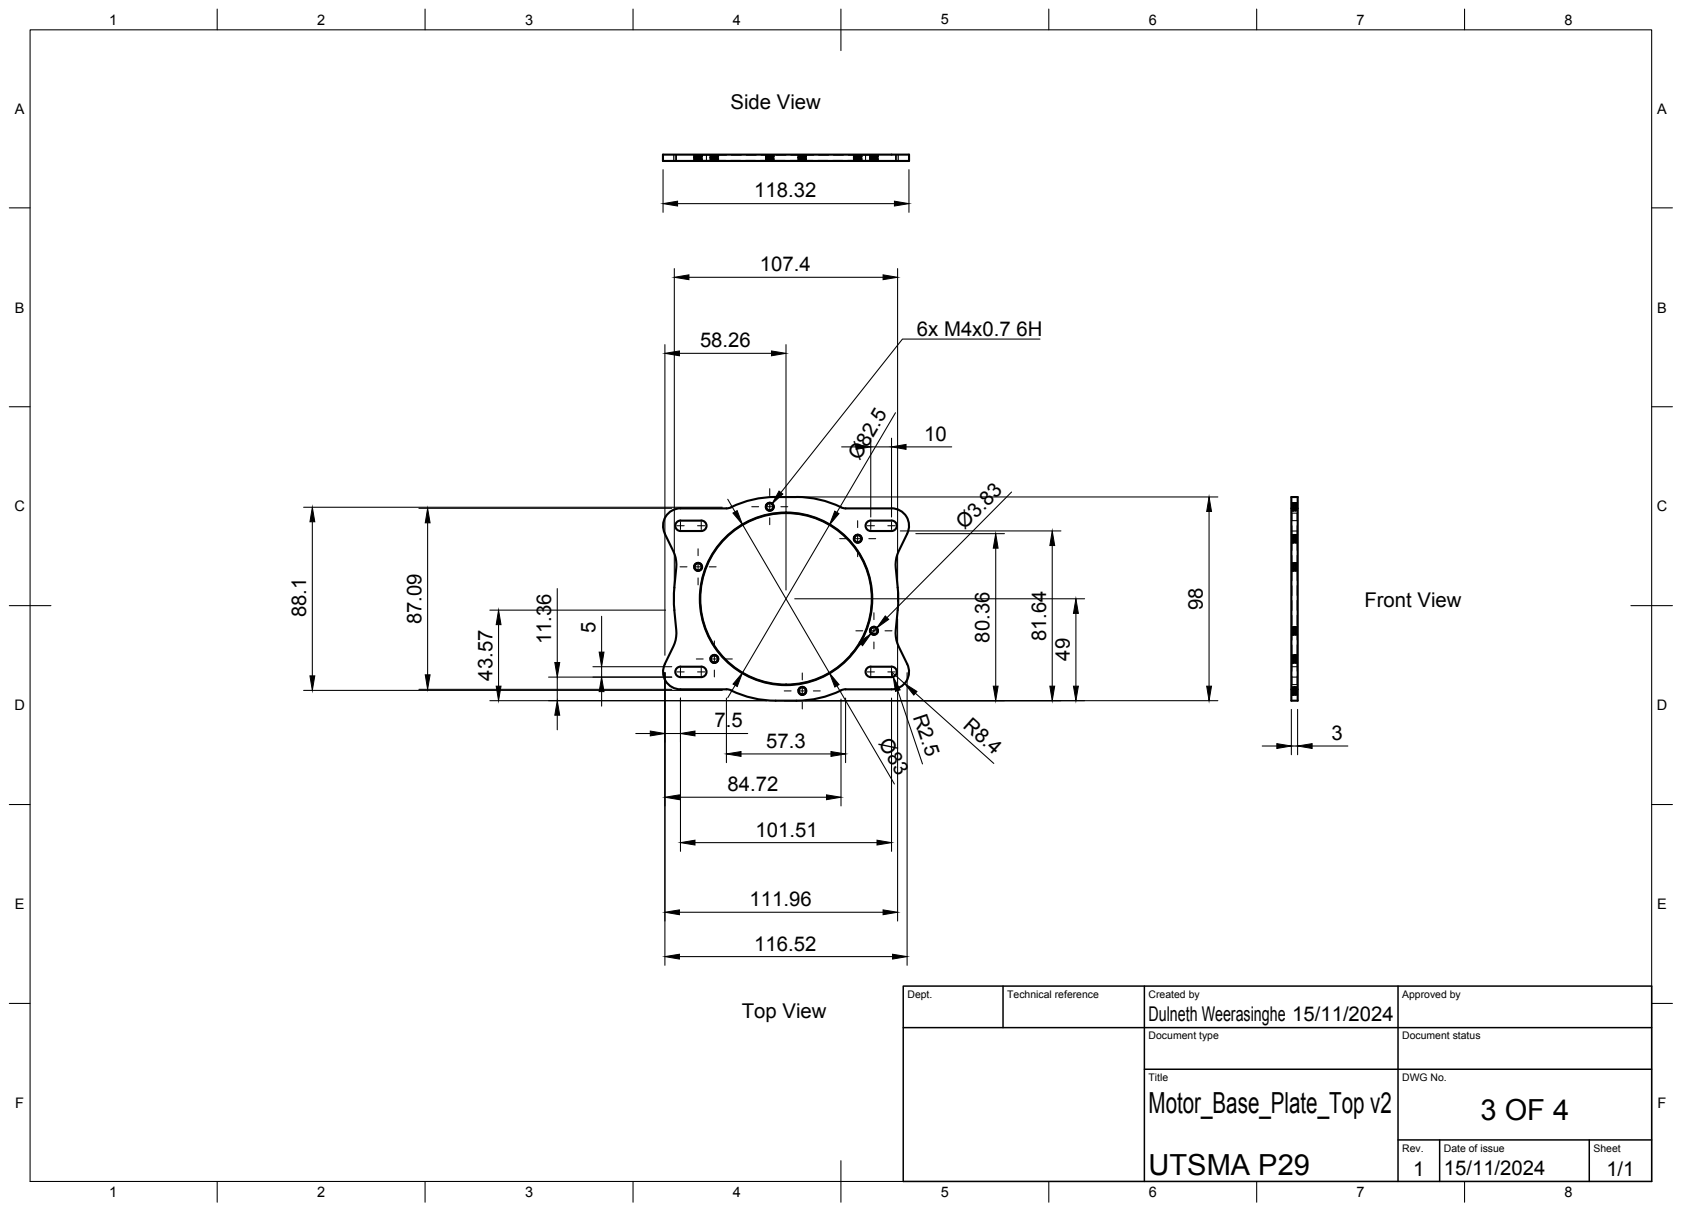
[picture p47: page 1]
Title; DWG No.; Rev.; Date of issue; Sheet; UTSMA P29; Motor_Base_Plate_Top v2; Side View; Front View; Top View

Dept. | Technical reference | Created by Dulneth Weerasinghe 15/11/2024 | Approved by

Document type | Document status

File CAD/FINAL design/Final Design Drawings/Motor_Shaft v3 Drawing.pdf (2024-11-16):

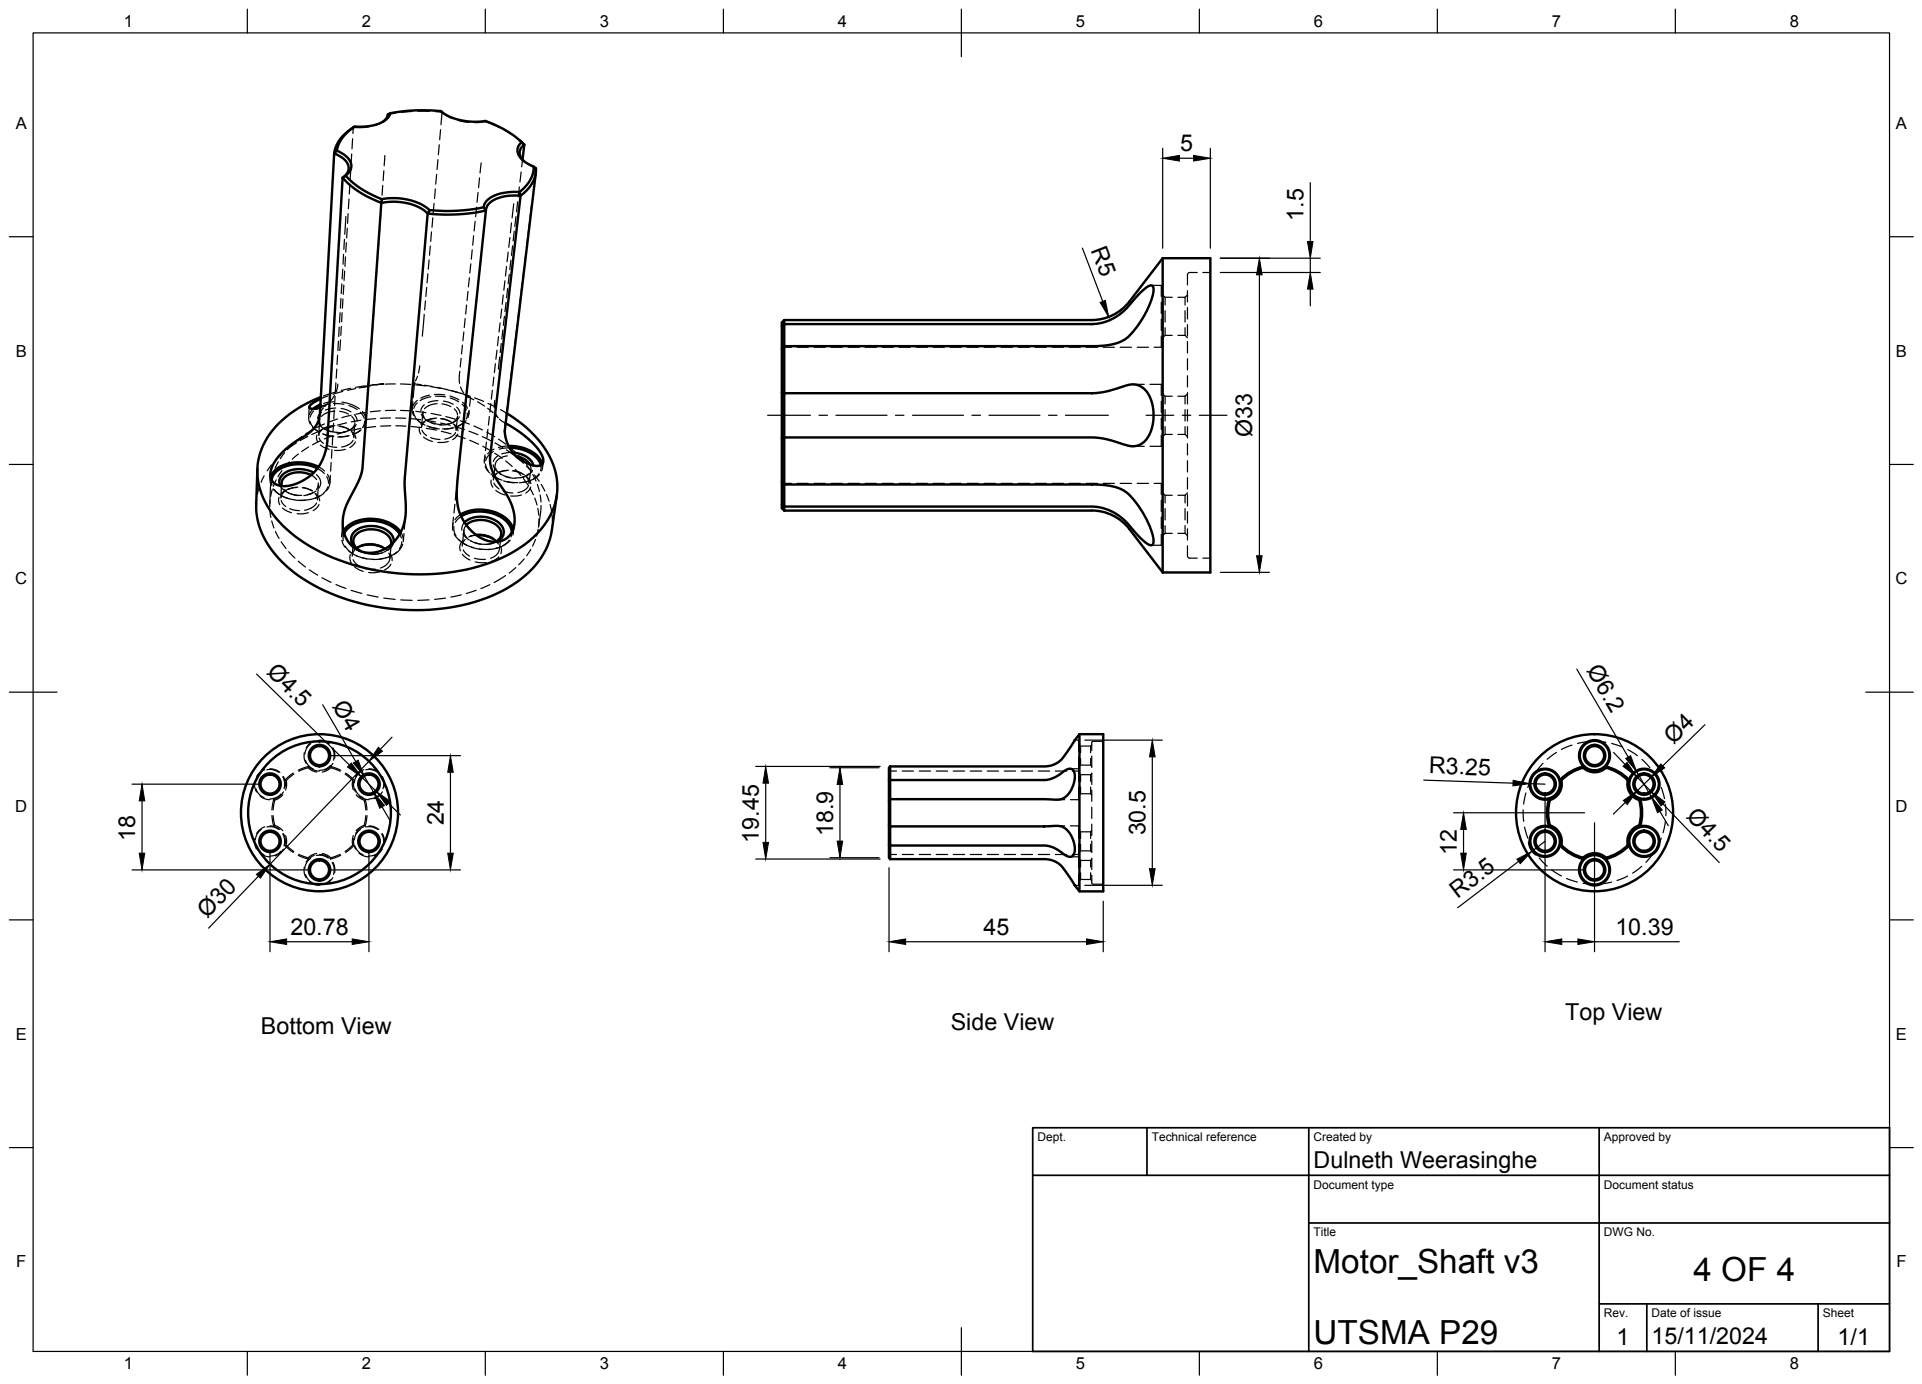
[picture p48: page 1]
Title; DWG No.; Rev.; Date of issue; Sheet; UTSMA P29; Motor_Shaft v3; Dulneth Weerasinghe 24; Bottom View; Side View; Top View

Dept. | Technical reference | Created by | Approved by

Document type | Document status

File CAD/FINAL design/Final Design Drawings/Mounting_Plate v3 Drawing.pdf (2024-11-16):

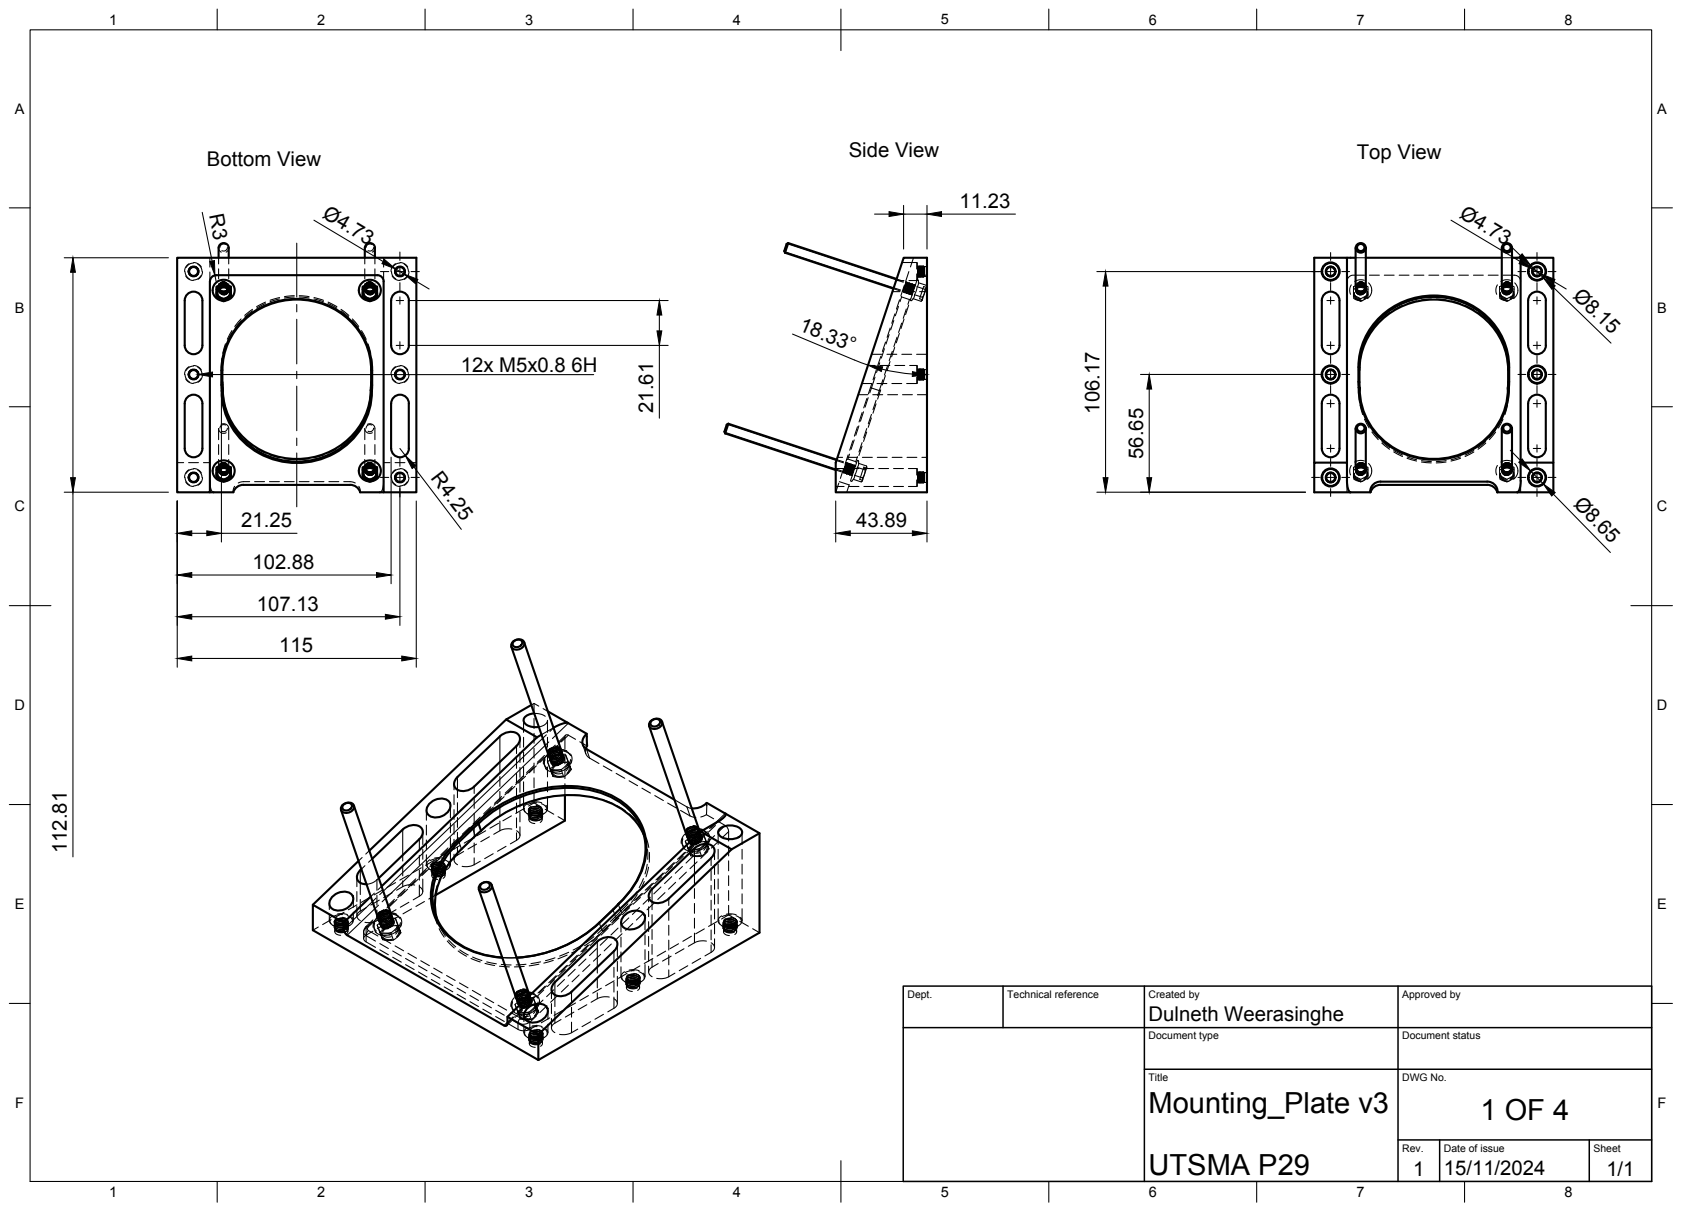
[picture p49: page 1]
Title; DWG No.; Rev.; Date of issue; Sheet; UTSMA P29; Mounting_Plate v3; Side View; Top View Bottom View

Dept. | Technical reference | Created by Dulneth Weerasinghe | Approved by

Document type | Document status

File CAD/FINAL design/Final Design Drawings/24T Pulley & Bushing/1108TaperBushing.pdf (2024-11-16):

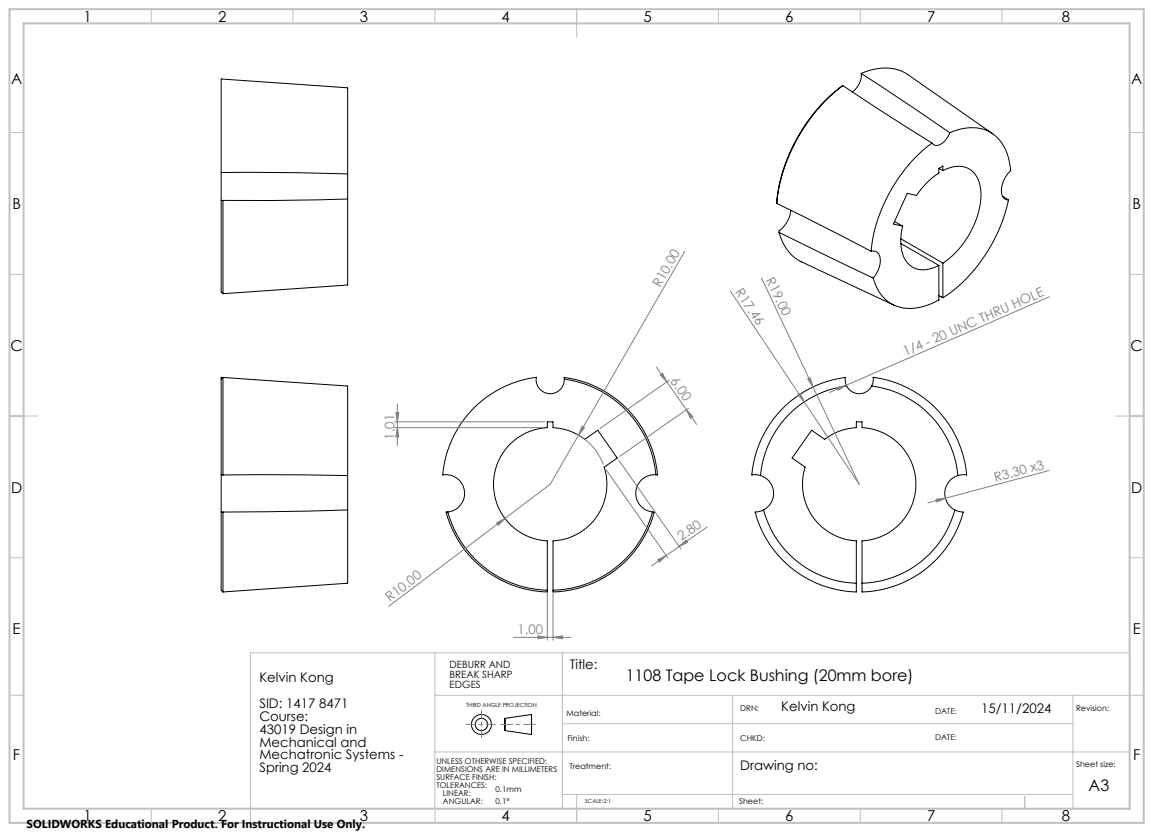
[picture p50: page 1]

1/4 - 20 UNC THRU HOLE

Kelvin Kong SID: 1417 8471 Course: 43019 Design in Mechanical and Mechatronic Systems -Spring 2024 | DEBURR AND BREAK SHARP EDGES | Title: 1108 Tape Lock Bushing (20mm bore)

THIRD ANGLE PROJECTION | Material: | Kelvin Kong 15/11/2024 DRN: DATE: | Revision:

Finish: | CHKD: DATE:

UNLESS OTHERWISE SPECIFIED: DIMENSIONS ARE IN MILLIMETERS SURFACE FINISH: TOLERANCES: 0.1mm LINEAR: ANGULAR: 0.1° | Treatment: | Drawing no: | Sheet size: A3

SCALE:2:1 | Sheet:

SOLIDWORKS Educational Product. For Instructional Use Only.

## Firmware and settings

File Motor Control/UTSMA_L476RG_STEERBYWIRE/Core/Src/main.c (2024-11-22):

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
/* Includes ------------------------------------------------------------------*/
#include "main.h"

/* USER CODE BEGIN Includes */
#define PUTCHAR_PROTOTYPE int __io_putchar(int ch)
#include "cubemars_control.h"

/* USER CODE END Includes */

ADC_HandleTypeDef hadc1;

CAN_HandleTypeDef hcan1;

TIM_HandleTypeDef htim2;
TIM_HandleTypeDef htim3;
TIM_HandleTypeDef htim4;
TIM_HandleTypeDef htim8;
TIM_HandleTypeDef htim16;

UART_HandleTypeDef huart2;

/* USER CODE BEGIN PV */
int value;
int value_2;

int adcValue;
GPIO_PinState buttonValue;

// CAN IDs
uint32_t CAN_SENDER_ID = 4; // for sending command
int      CAN_LISTEN_ID = 4; // for listening to reply

// Variables for sending motor command
float Pos_ref;
float Vel_ref = 0;
float Kp = 0.5;
float Kd = 0.2;
float Trq_ff = 0;

// Variables for receiving motor message
float position, speed, torque, temperature;
mc_fault_code error;

/* USER CODE END PV */

void SystemClock_Config(void);
static void MX_GPIO_Init(void);
static void MX_USART2_UART_Init(void);
static void MX_CAN1_Init(void);
static void MX_ADC1_Init(void);
static void MX_TIM2_Init(void);
static void MX_TIM3_Init(void);
static void MX_TIM4_Init(void);
static void MX_TIM8_Init(void);
static void MX_TIM16_Init(void);
/* USER CODE BEGIN PFP */


CAN_FilterTypeDef sFilterConfig;
CAN_TxHeaderTypeDef TxHeader;
CAN_RxHeaderTypeDef RxHeader;
uint8_t TxData[8];
uint8_t RxData[8];
uint32_t TxMailbox;
int increment = 0;

long map(long x, long in_min, long in_max, long out_min, long out_max);

/* USER CODE END PFP */

/**
  * @brief  The application entry point.
  * @retval int
  */
int main(void)
{
  /* MCU Configuration--------------------------------------------------------*/

  /* Reset of all peripherals, Initializes the Flash interface and the Systick. */
  HAL_Init();

  /* Configure the system clock */
  SystemClock_Config();

  /* Initialize all configured peripherals */
  MX_GPIO_Init();
  MX_USART2_UART_Init();
  MX_CAN1_Init();
  MX_ADC1_Init();
  MX_TIM2_Init();
  MX_TIM3_Init();
  MX_TIM4_Init();
  MX_TIM8_Init();
  MX_TIM16_Init();
  /* USER CODE BEGIN 2 */


  sFilterConfig.FilterActivation = CAN_FILTER_ENABLE;
  sFilterConfig.FilterBank = 10;  // anything between 0 to SlaveStartFilterBank
  sFilterConfig.FilterFIFOAssignment = CAN_RX_FIFO0;
  sFilterConfig.FilterIdHigh = 0;
  sFilterConfig.FilterIdLow = 0x0000;
  sFilterConfig.FilterMaskIdHigh = 0;
  sFilterConfig.FilterMaskIdLow = 0x0000;
  sFilterConfig.FilterMode = CAN_FILTERMODE_IDMASK;
  sFilterConfig.FilterScale = CAN_FILTERSCALE_32BIT;
  sFilterConfig.SlaveStartFilterBank = 0;  // 13 to 27 are assigned to slave CAN (CAN 2) OR 0 to 12 are assgned to CAN1


//  sFilterConfig.FilterBank=0;
//  sFilterConfig.FilterMode=CAN_FILTERMODE_IDMASK;
//  sFilterConfig.FilterScale=CAN_FILTERSCALE_32BIT;
//  sFilterConfig.FilterIdHigh=0x0000;
//  sFilterConfig.FilterIdLow=0x0000;
//  sFilterConfig.FilterMaskIdHigh=0x0000;
//  sFilterConfig.FilterMaskIdLow=0x0000;
//  sFilterConfig.FilterFIFOAssignment=CAN_RX_FIFO0;
//  sFilterConfig.FilterActivation=ENABLE;
//  sFilterConfig.SlaveStartFilterBank=14;


  if(HAL_CAN_ConfigFilter(&hcan1,&sFilterConfig)!=HAL_OK)
  {
	  /* Filter configuration Error */ Error_Handler();

  }

  if(HAL_CAN_Start(&hcan1)!=HAL_OK)
  {
	  /* Start Error */ Error_Handler();
  }

  if(HAL_CAN_ActivateNotification(&hcan1,CAN_IT_RX_FIFO0_MSG_PENDING |CAN_IT_TX_MAILBOX_EMPTY)!=HAL_OK)
  {
	  /* Notification Error */ Error_Handler();
  }


  TxHeader.StdId=CAN_SENDER_ID; // 0x201
  TxHeader.ExtId=0;
  TxHeader.RTR=CAN_RTR_DATA;
  TxHeader.IDE=CAN_ID_STD;
  TxHeader.DLC=8;
  TxHeader.TransmitGlobalTime=DISABLE;

  //TxData[0]=0; TxData[1]=0; TxData[2]=0; TxData[3]=0; TxData[4]=0; TxData[5]=1; TxData[6]=1; TxData[7]=1;
  //HAL_CAN_AddTxMessage(&hcan1,&TxHeader,TxData,&TxMailbox);



  HAL_ADC_Start(&hadc1);

  /* USER CODE END 2 */

  /* Infinite loop */
  /* USER CODE BEGIN WHILE */
  while (1)
  {
	  // /* Read potentiometer value
	  if (HAL_ADC_PollForConversion(&hadc1, 100) == HAL_OK) { // Wait up to 100ms
	      adcValue = HAL_ADC_GetValue(&hadc1);
	      //printf("ADC Value: %d\n", adcValue);
	  } else {
	      printf("ADC Conversion Timeout or Error\n");
	  }
	  HAL_ADC_Start(&hadc1); // Restart ADC to be ready for next measurement
	  // */

	  // Read state of blue button
	  buttonValue = HAL_GPIO_ReadPin(RES_BUTTON_GPIO_Port, RES_BUTTON_Pin);

	  // /* Simple transmission to test connection between MCUs
	  adcValue = map(adcValue, 0, 4095, 0, 255);
	  TxData[0] = adcValue;
	  TxData[1] = increment++;
	  TxData[2] = 123;
	  TxData[3] = buttonValue;
	  HAL_CAN_AddTxMessage(&hcan1, &TxHeader, TxData, &TxMailbox);
	  // */

	  /* Enter and exit Motor Control Mode to test connection
	  if (HAL_CAN_AddTxMessage(&hcan1, &TxHeader, CAN_CMD_ENTER_MOTOR_CONTROL_MODE, &TxMailbox) == HAL_OK) {
		  printf("Enter Command Sent.\n");
	  }
	  HAL_Delay(1000);
	  if (HAL_CAN_AddTxMessage(&hcan1, &TxHeader, CAN_CMD_EXIT_MOTOR_CONTROL_MODE, &TxMailbox) == HAL_OK) {
		  printf("Exit Command Sent.\n");
	  }
	  HAL_ADC_Start(&hadc1);
	  HAL_Delay(750);
	  */

	  /* Send command to motor
	  Pos_ref = map(adcValue, 0, 4095, 0, M_TWOPI);
	  Vel_ref = 0;
	  Kp = 0.5;
	  Kd = 0.2;
	  Trq_ff = 0; // 2 * (float)!HAL_GPIO_ReadPin(RES_BUTTON_GPIO_Port, RES_BUTTON_Pin); // Optionally, give the motor a 2Nm feedforward torque when button is pressed
	  cubemars_send_can_cmd(&hcan1, &TxHeader, &TxMailbox, Pos_ref, Vel_ref, Kp, Kd, Trq_ff);
	  */

	  HAL_Delay(250);

	  /// ORIGINAL VERSION BELOW ///
/*
//	  HAL_CAN_AddTxMessage(&hcan1,&TxHeader,TxData,&TxMailbox); //HAL_Delay(500);
//	  TxData[1] = value++;
//	  TxData[5] = value++;
//	  printf("CAN Tx: %d %d %d %d %d %d %d %d \r\n", TxHeader.StdId, TxData[0], TxData[1], TxData[2], TxData[3], TxData[4], TxData[5], TxData[6], TxData[7]);
//	  printf("CAN Rx: %d %d %d %d %d %d %d %d \r\n", RxHeader.StdId, RxData[0], RxData[1], RxData[2], RxData[3], RxData[4], RxData[5], RxData[6], RxData[7]);
	  //printf("Rx %d \r\n", value_2);

	  HAL_ADC_Start(&hadc1);
//
//
	  adcValue = map(HAL_ADC_GetValue(&hadc1), 0, 4095, 0, 255);
	  TxData[0] = adcValue;
	  TxData[1] = increment++;
	  TxData[2] = 123;
	  HAL_CAN_AddTxMessage(&hcan1, &TxHeader, TxData, &TxMailbox);
	  printf("CAN Tx: %d %d ADC Value %d \r\n", TxHeader.StdId, TxData[0], TxData[1], adcValue);
//	  printf("ADC Value: %d \r\n", adcValue);
	  HAL_Delay(250);
*/

    /* USER CODE END WHILE */

    /* USER CODE BEGIN 3 */
  }
  /* USER CODE END 3 */
}

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
/* USER CODE BEGIN 4 */
void HAL_CAN_TxMailbox0CompleteCallback(CAN_HandleTypeDef *hcan)
{
	//HAL_GPIO_TogglePin(GPIOC, GPIO_PIN_13);
	value_2++;
	//printf("Tx %d \r\n", value);

}

void HAL_CAN_RxFifo0MsgPendingCallback(CAN_HandleTypeDef *hcan)
{
	HAL_CAN_GetRxMessage(&hcan1,CAN_RX_FIFO0,&RxHeader,RxData);

	// Print raw data
	print_raw_data(RxData);

	// Process received message from motor
	//cubemars_get_can_msg(RxData, CAN_LISTEN_ID, &position, &speed, &torque, &temperature, &error);

	// Process received command, emulating a motor receiving the command (for debugging purposes)
	//cubemars_get_can_cmd4debug(RxData);

	// Light LD2 based on received data (for confirming connection)
	HAL_GPIO_WritePin(LD2_GPIO_Port, LD2_Pin, !RxData[3]);

	value++;
	//printf("Rx %d \r\n", value);
}


PUTCHAR_PROTOTYPE
{
  /* Place your implementation of fputc here */
  /* e.g. write a character to the USART1 and Loop until the end of transmission */
  HAL_UART_Transmit(&huart2, (uint8_t *)&ch, 1, 0xFFFF);

  return ch;
}

long map(long x, long in_min, long in_max, long out_min, long out_max) {
  return (x - in_min) * (out_max - out_min) / (in_max - in_min) + out_min;
}



/* USER CODE END 4 */
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


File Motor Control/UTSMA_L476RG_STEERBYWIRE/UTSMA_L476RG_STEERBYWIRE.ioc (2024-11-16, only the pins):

Mcu.UserName=STM32L476RGTx
PA0.Signal=S_TIM2_CH1
PA1.Signal=S_TIM2_CH2
PA2.GPIO_Label=USART_TX
PA2.Signal=USART2_TX
PA3.GPIO_Label=USART_RX
PA3.Signal=USART2_RX
PA5.GPIO_Label=LD2 [green Led]
PA5.Signal=GPIO_Output
PA6.Signal=S_TIM3_CH1
PA7.Signal=S_TIM3_CH2
PB6.Signal=S_TIM4_CH1
PB7.Signal=S_TIM4_CH2
PB8.Signal=CAN1_RX
PB9.Signal=CAN1_TX
PC0.GPIO_Label=Potentiometer
PC0.Signal=ADCx_IN1
PC13.GPIO_Label=RES_BUTTON
PC13.Signal=GPXTI13
PC6.Signal=S_TIM8_CH1
PC7.Signal=S_TIM8_CH2

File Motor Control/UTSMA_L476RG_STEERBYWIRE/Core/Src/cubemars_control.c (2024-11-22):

/**
 * @file cubemars_control.c
 * @brief Implementation of functions for controlling CubeMars motors via CAN communication.
 *
 * This source file implements the functions declared in cubemars_control.h.
 * It provides functionality for:
 * - Packing and sending control commands to CubeMars motors in MIT Control Mode.
 * - Receiving and unpacking feedback from the motors.
 * - Printing motor states and error information for debugging.
 *
 * Dependencies:
 * - STM32 HAL library (for CAN communication).
 * - The CubeMars motor manual for parameter ranges and command details.
 *
 * Many of the functions in this document are based on example code in the
 * AK Series Module Driver User Manual V1.0.15.X, as referenced in the function comments below.
 *
 * Setup:
 * - Initialize the CAN peripheral before calling these functions.
 * - Ensure proper configuration of the CAN bus (baud rate, filters, etc.).
 *
 * Note:
 * Floating-point support for `printf` is required to print motor data and debugging information.
 *
 * Developed for UTS Motorsports Autonomous
 * Project 29 by Team 21
 * 43019 Design in Mechanical and Mechatronic Systems
 * University of Technology Sydney
 * November 2024
 */

#include "cubemars_control.h"

// Special CAN Commands
const uint8_t CAN_CMD_ENTER_MOTOR_CONTROL_MODE[8] = {0xFF, 0xFF, 0xFF, 0xFF, 0xFF, 0xFF, 0xFF, 0xFC};
const uint8_t CAN_CMD_EXIT_MOTOR_CONTROL_MODE[8]  = {0xFF, 0xFF, 0xFF, 0xFF, 0xFF, 0xFF, 0xFF, 0xFD};
const uint8_t CAN_CMD_SET_ORIGIN[8]               = {0xFF, 0xFF, 0xFF, 0xFF, 0xFF, 0xFF, 0xFF, 0xFE};
const uint8_t CAN_CMD_READ_STATE[8]               = {0xFF, 0xFF, 0xFF, 0xFF, 0xFF, 0xFF, 0xFF, 0xFC};

// Parameter Ranges
const float P_MIN =-12.5f;
const float P_MAX = 12.5f;
const float V_MIN =-50.0f;
const float V_MAX = 50.0f;
const float T_MIN =-18.0f;
const float T_MAX = 18.0f;
const float KP_MIN = 0;
const float KP_MAX = 500.0f;
const float KD_MIN = 0;
const float KD_MAX = 5.0f;

/**
 * @brief Converts a float value into an unsigned integer within a specified range and resolution. (AK Series User Manual, p. 44)
 *
 * @param x The input float value to convert.
 * @param x_min The minimum value of the range.
 * @param x_max The maximum value of the range.
 * @param bits The number of bits used to represent the unsigned integer.
 * @return The converted unsigned integer value.
 */
int float_to_uint(float x, float x_min, float x_max, unsigned int bits) {
	/// Converts a float to an unsigned int, given range and number of bits ///
	float span = x_max - x_min;
	if(x < x_min) x = x_min;
	else if(x > x_max) x = x_max;
	return (int) ((x - x_min) * ((float)((1 << bits) / span)));
}

/**
 * @brief Converts an unsigned integer into a float within a specified range and resolution. (AK Series User Manual, p. 44)
 *
 * @param x_int The input unsigned integer to convert.
 * @param x_min The minimum value of the range.
 * @param x_max The maximum value of the range.
 * @param bits The number of bits used to represent the unsigned integer.
 * @return The converted float value.
 */
float uint_to_float(int x_int, float x_min, float x_max, unsigned int bits) {
	/// converts unsigned int to float, given range and number of bits ///
	float span = x_max - x_min;
	float offset = x_min;
	return ((float)x_int) * span / ((float)((1 << bits) - 1)) + offset;
}

/**
 * @brief Packs control parameters into an 8-byte CAN data buffer for transmission. (AK Series User Manual, p. 43)
 *
 * @param data The 8-byte CAN data buffer.
 * @param p_des Desired position.
 * @param v_des Desired speed.
 * @param kp Proportional gain.
 * @param kd Derivative gain.
 * @param t_ff Feedforward torque.
 */
void pack_cmd(uint8_t data[8], float p_des, float v_des, float kp, float kd, float t_ff) {
	/// limit data to be within bounds ///
	p_des = fminf(fmaxf(P_MIN, p_des), P_MAX);
	v_des = fminf(fmaxf(V_MIN, v_des), V_MAX);
	kp = fminf(fmaxf(KP_MIN, kp), KP_MAX);
	kd = fminf(fmaxf(KD_MIN, kd), KD_MAX);
	t_ff = fminf(fmaxf(T_MIN, t_ff), T_MAX);

	/// convert floats to unsigned ints ///
	int p_int =  float_to_uint(p_des,  P_MIN,  P_MAX, 16);
	int v_int =  float_to_uint(v_des,  V_MIN,  V_MAX, 12);
	int kp_int = float_to_uint(   kp, KP_MIN, KP_MAX, 12);
	int kd_int = float_to_uint(   kd, KD_MIN, KD_MAX, 12);
	int t_int =  float_to_uint( t_ff,  T_MIN,  T_MAX, 12);

	/// pack ints into the can buffer ///
	data[0] = p_int >> 8; 							// Position High 8
	data[1] = p_int & 0xFF; 						// Position Low 8
	data[2] = v_int >> 4; 							// Speed High 8 bits
	data[3] = ((v_int & 0xF) << 4) | (kp_int >> 8);	// Speed Low 4 bits KP High 4 bits
	data[4] = kp_int & 0xFF; 						// KP Low 8 bits
	data[5] = kd_int >> 4; 							// Kd High 8 bits
	data[6] = ((kd_int & 0xF) << 4) | (t_int >> 8); // KP Low 4 bits Torque High 4 bits
	data[7] = t_int & 0xFF; 						// Torque Low 8 bits
}

/**
 * @brief Sends a command to the CubeMars motor via CAN.
 *
 * @param hcan Pointer to the CAN handle.
 * @param TxHeader Pointer to the CAN TxHeader structure.
 * @param TxMailbox Pointer to the mailbox identifier for transmission.
 * @param p_des Desired position.
 * @param v_des Desired speed.
 * @param kp Proportional gain.
 * @param kd Derivative gain.
 * @param t_ff Feedforward torque.
 */
void cubemars_send_can_cmd(CAN_HandleTypeDef *hcan, CAN_TxHeaderTypeDef *TxHeader, uint32_t *TxMailbox, float p_des, float v_des, float kp, float kd, float t_ff) {
	// Convert and pack data
	uint8_t data[8];
	pack_cmd(data, p_des, v_des, kp, kd, t_ff);

	// Enter Motor Control Mode
	if (HAL_CAN_AddTxMessage(hcan, TxHeader, CAN_CMD_ENTER_MOTOR_CONTROL_MODE, TxMailbox) != HAL_OK) {
		// Handle error (optional: print error or use debugging tools)
		printf("Error: Failed to send Enter Motor Control Mode command.\n");
	}

	// Send position, speed, and control parameters
	if (HAL_CAN_AddTxMessage(hcan, TxHeader, data, TxMailbox) != HAL_OK) {
		// Handle error (optional: print error or use debugging tools)
		printf("Error: Failed to send motor control command.\n");
	}
}
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

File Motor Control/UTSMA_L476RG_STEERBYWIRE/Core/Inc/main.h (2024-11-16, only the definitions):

#define RES_BUTTON_Pin GPIO_PIN_13
#define RES_BUTTON_GPIO_Port GPIOC
#define Potentiometer_Pin GPIO_PIN_0
#define Potentiometer_GPIO_Port GPIOC
#define USART_TX_Pin GPIO_PIN_2
#define USART_TX_GPIO_Port GPIOA
#define USART_RX_Pin GPIO_PIN_3
#define USART_RX_GPIO_Port GPIOA
#define LD2_Pin GPIO_PIN_5
#define LD2_GPIO_Port GPIOA
#define TMS_Pin GPIO_PIN_13
#define TMS_GPIO_Port GPIOA
#define TCK_Pin GPIO_PIN_14
#define TCK_GPIO_Port GPIOA
#define SWO_Pin GPIO_PIN_3
#define SWO_GPIO_Port GPIOB

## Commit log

2024-11-16 Initial project commit
    [1108TaperBushing.SLDDRW, 1610 TLBushing T31074.SLDDRW, 17510500.SLDPRT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]
2024-11-20 Ready for handover
    [Motor Mount Scoring Matrix.xlsx, Scoring Matrix.xlsx]

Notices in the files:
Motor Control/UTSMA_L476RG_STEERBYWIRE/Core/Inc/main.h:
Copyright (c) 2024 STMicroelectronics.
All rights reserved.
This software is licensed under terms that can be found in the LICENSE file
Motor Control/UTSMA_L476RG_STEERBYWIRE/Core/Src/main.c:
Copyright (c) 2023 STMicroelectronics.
